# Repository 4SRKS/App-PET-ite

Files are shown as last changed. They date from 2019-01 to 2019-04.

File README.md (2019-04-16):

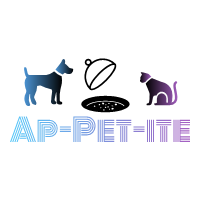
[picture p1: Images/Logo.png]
<br/>
## Social Media Profiles<br/>
[**Youtube**](https://www.youtube.com/channel/UCCG3uzNam2p5G15IFZl3F-A) 
[**Facebook**](https://www.facebook.com/Ap-PET-ite-2111281949162044/?view_public_for=2111281949162044)<br/>

## Project Overveiw<br/>
The basic layout of the project is given in the figure below<br/>
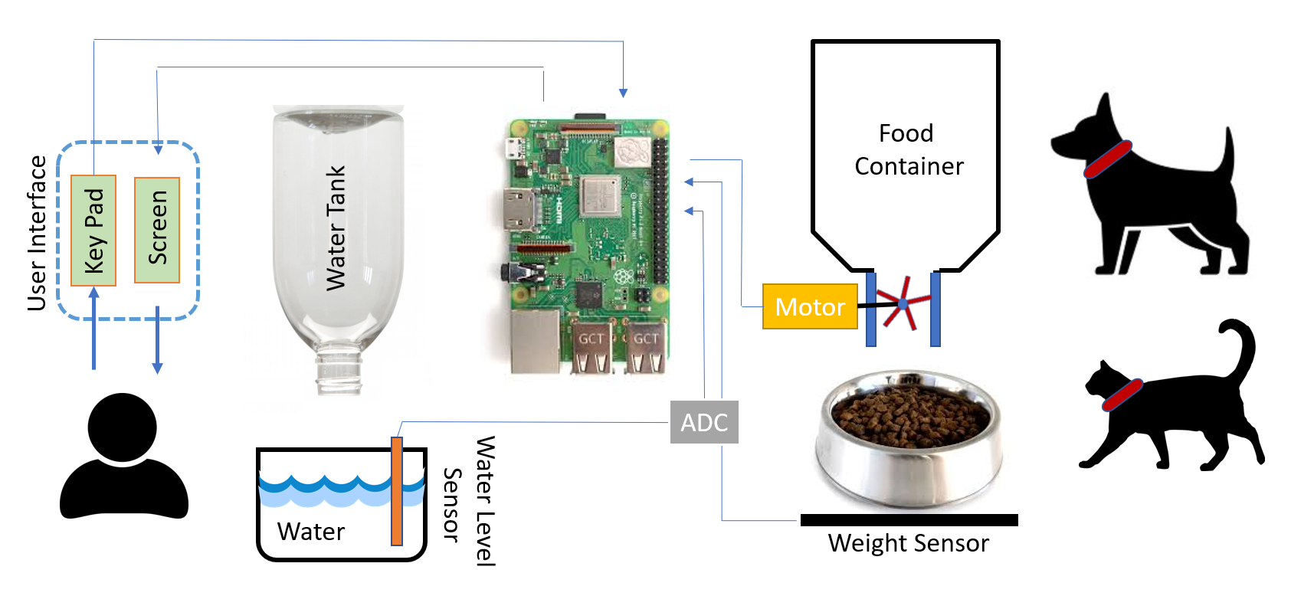
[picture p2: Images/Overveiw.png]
<br/>

## Project Description<br/>
The schematic above provides an overview of the project concept. The central component of the project design is a Raspberry Pi. The Pi is connected to peripheral devices that are used to control the food for a given Pet. The concept is not Pet specific and can be used to make an Automatic feeder for popular pets like cats or dogs and other smaller pets. The design includes two analog sensors to measure the weight and the water level. These sensors are connected to the Raspberry Pi through an ADC. SPI communication protocol is used to get analog values from the two sensors. A DC motor is controlled using a motor drive circuit. The user can interact with the Automatic Pet feeder through a user interface.<br/> 

## Component List<br/>
For this DIY project, we are using the Raspberry pi 3 Model B+ along with the following [Component List](https://github.com/RabiyaF/App-PET-ite/wiki/Component-List).<br/> <br/>
**Mechcanical Components List**<br/>
**1)** One DC Motor [6 Volts-150 RPM]<br/>
**2)** One Pet Food Bowl<br/> 
**3)** Wooden Planks<br/><br/>
**Electrical Components List** <br/>
**1)** One Analog water sensor<br/>
**2)** One Analog-to-digital Converter [MCP3008] <br/>
**3)** One 4x4 Matrix Keypad <br/>
**4)** One Analog Weight Sensor [HX711] with a maximum weight of 2 kgs <br/>
**5)** Five 1K Resistors <br/>
**6)** One TIP 122 or TIP 121 (NPN Transistor) <br/>
**7)** One LED <br/>
**8)** One Diode 1N4004 <br/>
**9)** Connector wires (F-F, M-F)<br/>
**10)** Two 20 Pin Female Connectors with a spacing of 0.1 in <br/>
**11)** One 8 pin Male connector with a spacing of 0.1 in <br/> 
**12)** One 4 pin Male connector with a spacing of 0.1 in <br/>
**13)** One 3 pin Male connector with a spacing of 0.1 in <br/>
**14)** One 16 pin IC holder with a spacing of 0.1 in between legs <br/>
After the Mechanical and Electrical Components have been procured, The following steps need to be followed to assemble App-PET-ite<br/>

# The Assembly 
## Mechanical Design Assembly <br/>
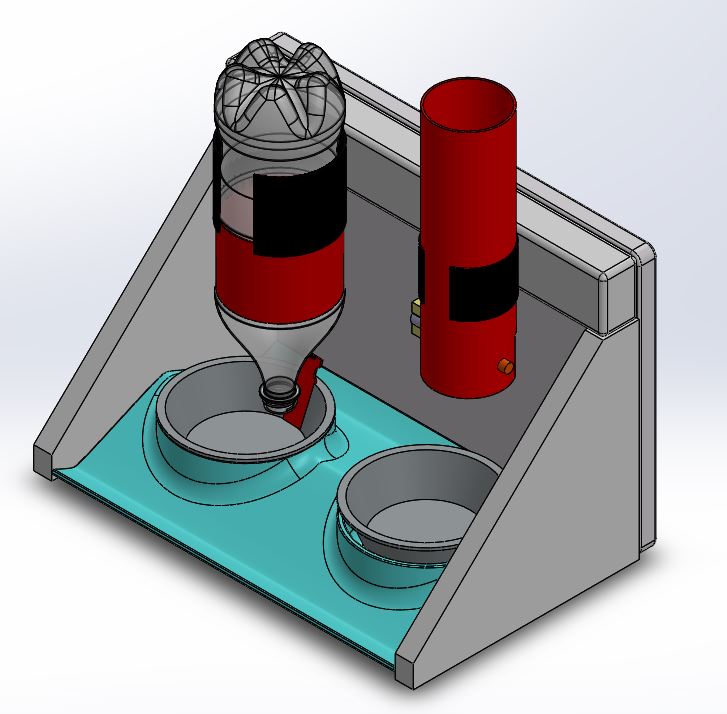
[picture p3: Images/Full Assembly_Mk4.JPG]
 <br/>
 <br/>
Shown above are a screenshot of the 3D CAD model and a photo of the final mechanical assembly.  The frame is made simply out of wood, and the clamps for the food and water tanks are made out of rigid PVC pipe with slots made in one side.  Everything else non-electrical is easily sourced in most supermarkets.  

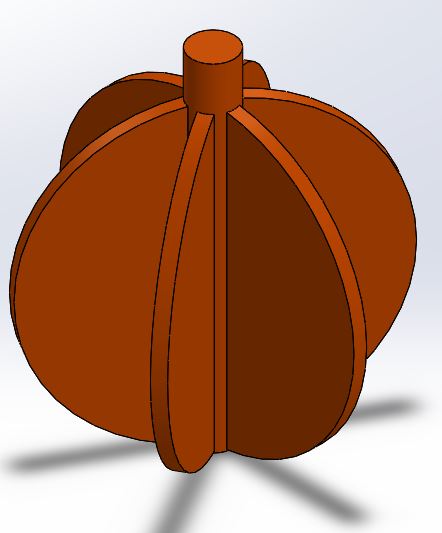
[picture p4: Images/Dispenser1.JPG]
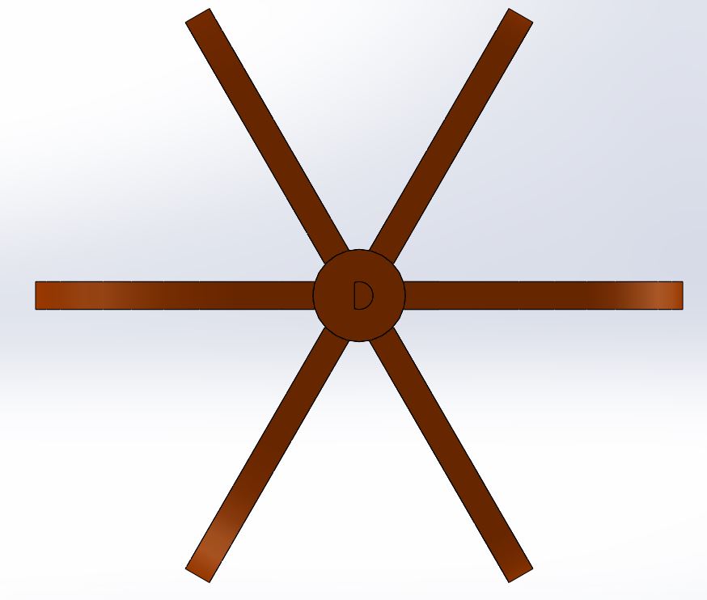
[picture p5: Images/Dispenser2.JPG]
 <br/>
The only other part requiring significant manufacturing is the dispenser mechanism, which was 3D printed.  Shown above are screenshots of this part.  For the .stl file of this component and the SolidWorks files of all the components shown in the full assembly, see the [SolidWorks/Mark 4](https://github.com/RabiyaF/App-PET-ite/tree/master/Solidworks/Mark%204) repository.  

For a full walkthrough of how we assembled the feeder, see the [Step-by-Step Assembly](https://github.com/RabiyaF/App-PET-ite/wiki/Step-by-Step-Mechanical-Assembly) page. <br/>

## Electrical Design Assembly <br/>
The first step of the electrical assembly is the PCB Fabrication.
### PCB Design <br/>
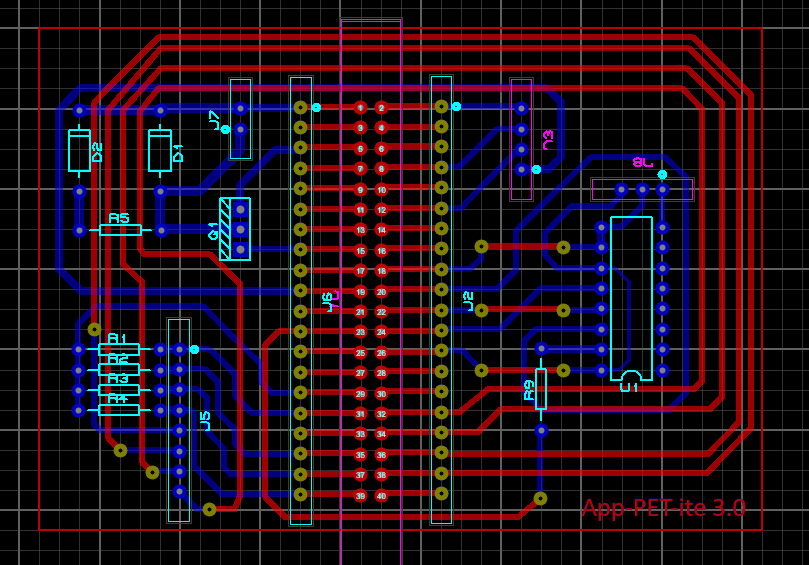
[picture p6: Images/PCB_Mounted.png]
<br/>
The figure above gives a preveiw of the PCB design. It is a double layered PCB Design. It includes the circuitry for Water Level Sensor, the ADC (MCP3008), the load cell (HX711), the key pad and the motordrive circuit. The PCB can be fabricated by printing the pdf files in the Double sided PCB folder and then using that layout to make a PCB step-by-step. A tutorial to make a PCB can be found at the following link. For a doubled layered PCB design the alignment of the two layers must be perfect. While aligning PCB use the text on the bottom as a guide to align the top and bottom halves. For a double sided PCB the process discribed in the tutorial must be repeated twice.<br/>
```
https://maker.pro/pcb/tutorial/how-to-make-a-printed-circuit-board-pcb
```
### Fabricated PCB<br/>
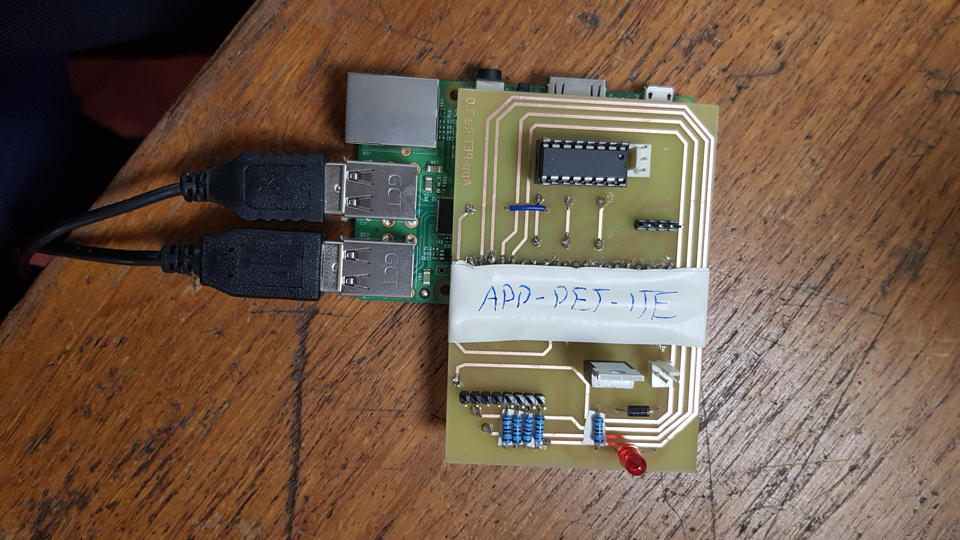
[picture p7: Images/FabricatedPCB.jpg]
<br/>

### Schematic<br/>
The figure below gives the schematic on which the PCB design is based.<br/>
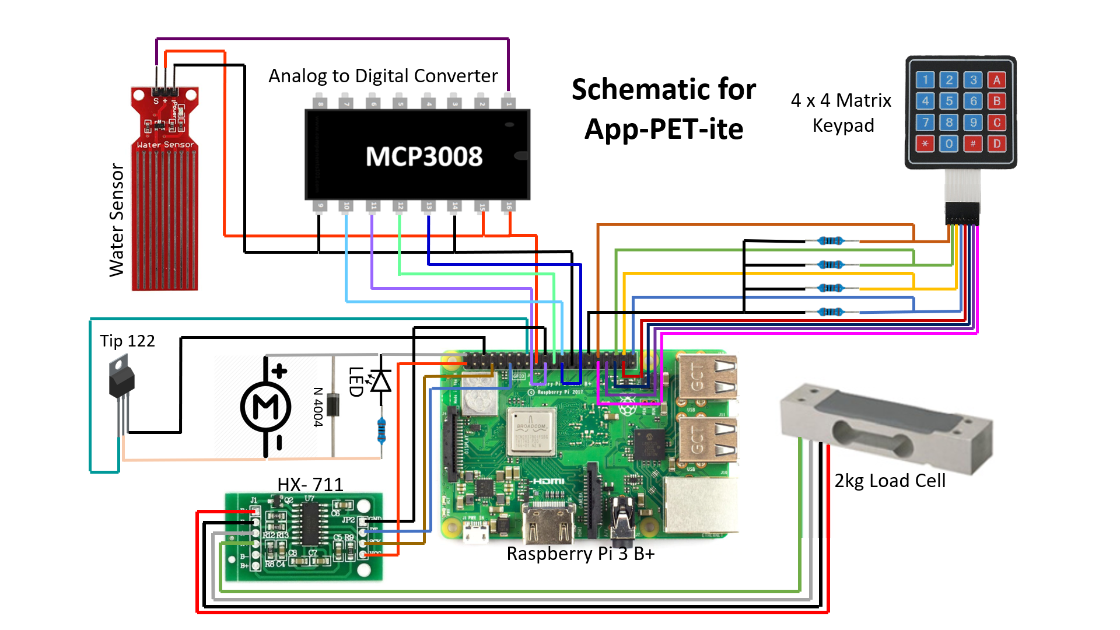
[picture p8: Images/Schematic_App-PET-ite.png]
<br/>

### Electrical Connections<br/>
A summary of the electrical connection is given below. <br/> 
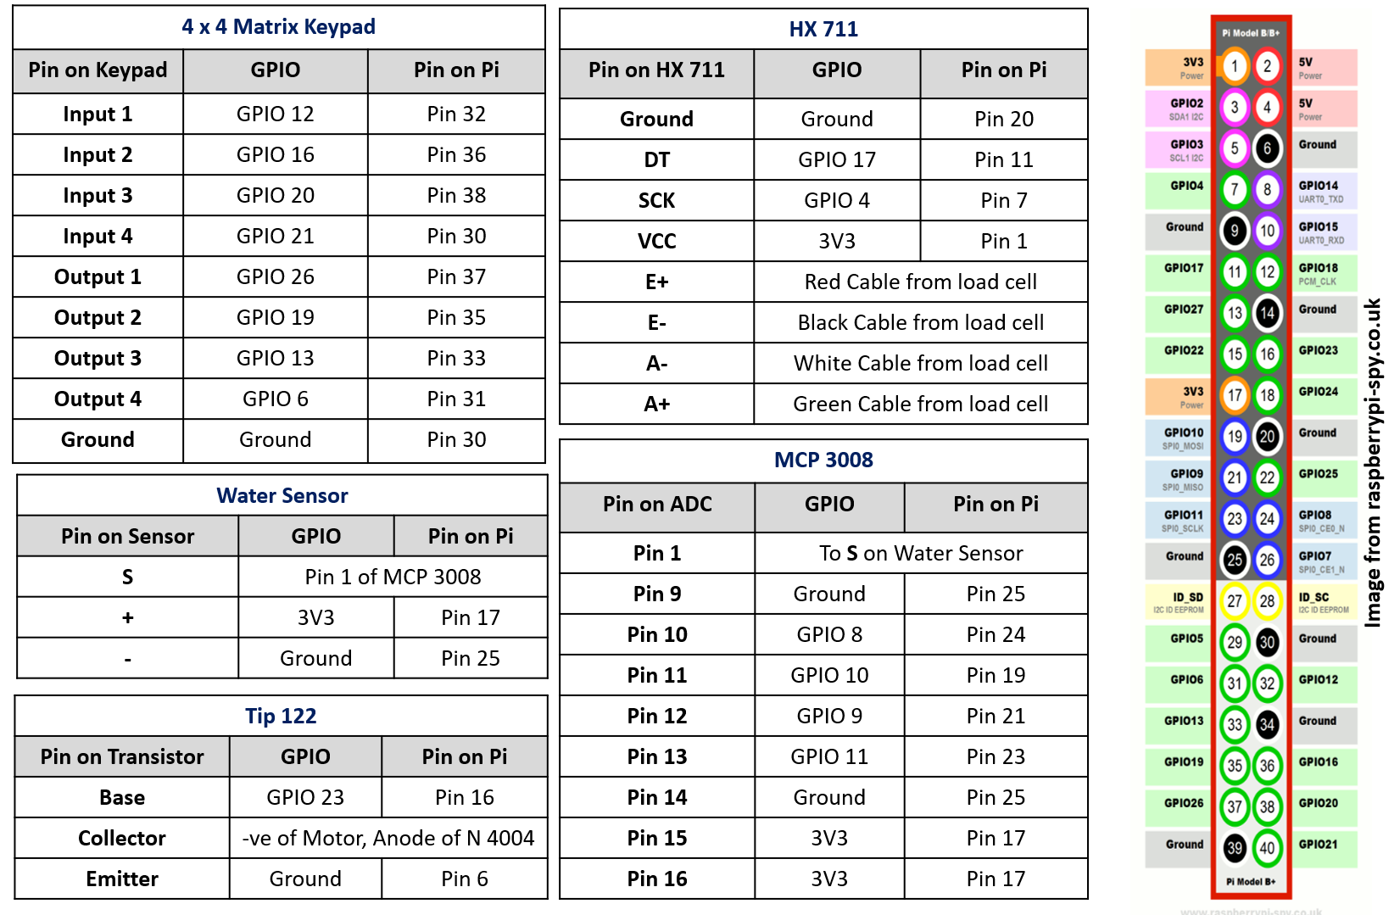
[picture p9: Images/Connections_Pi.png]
<br/>

## Ensuring Safety of Pet<br/>
Because of the nature of the project, It is recommneded to use the PCB layouts rather than using the schematic to build the circuit on a breadboard. All the wires must be taped down and all the electrical components should be out of the reach of the Pet. 

## Flowchart<br/>
The Flow chart below gives the overveiw of the code. First, the user initializes App-PET-ite with inputs for weight and time between two subsequent feeding times. The food is then dispensed based on user input. Then two threads run simulataneously. One counts down to the next time food is to be dispensed. The other thread periodically measures the Water level.  
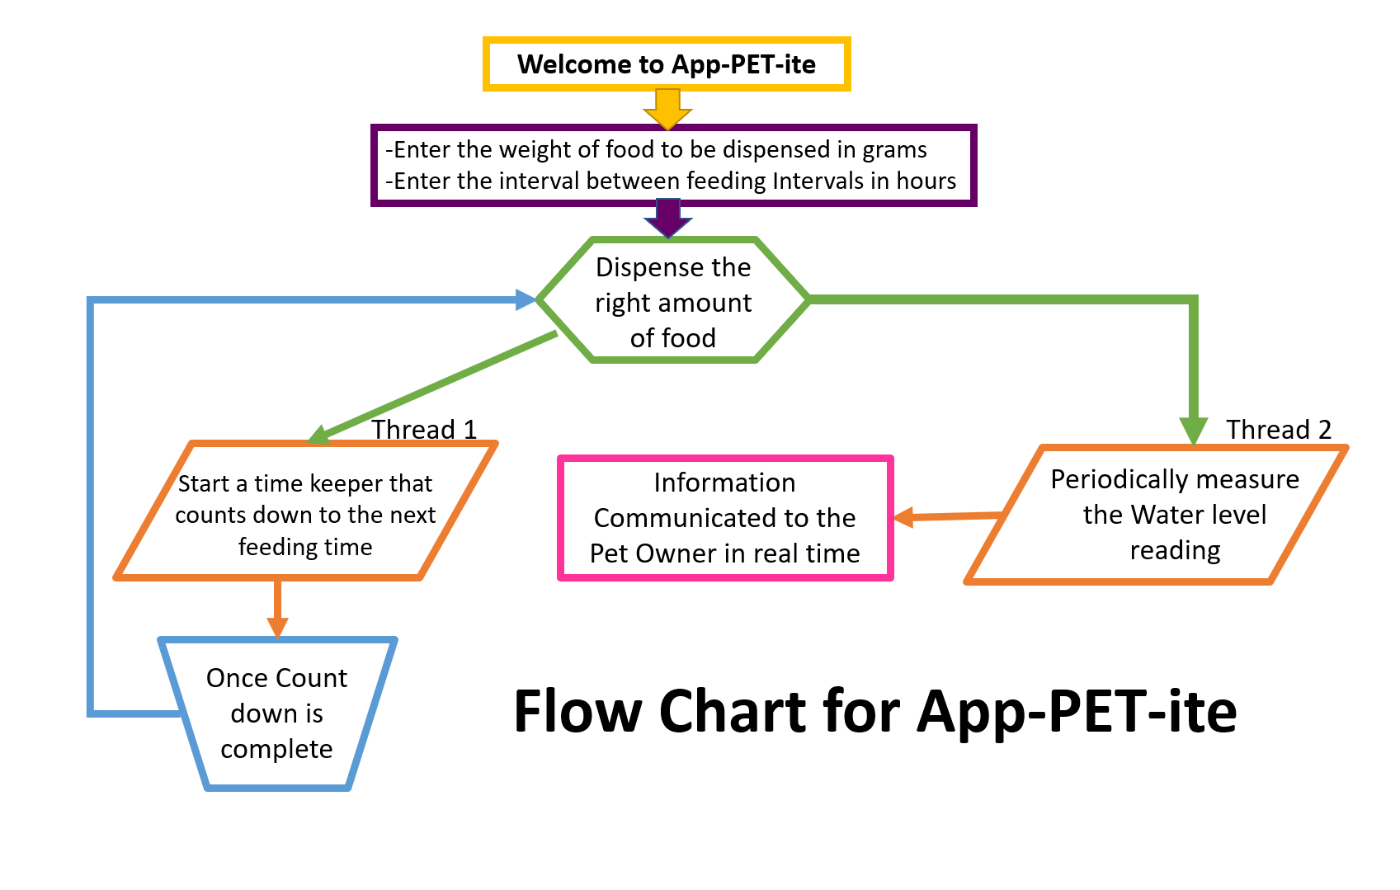
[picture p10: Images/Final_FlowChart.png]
<br/>

## Install the following packages using sudo apt-get <package name>
```
git 2.21.0
cmake-3.14.2.tar.gz
Qt 4.8.7
```
## To Run
```
git clone https://github.com/RabiyaF/App-PET-ite
cd Final_codes/build
cmake ..
make
./mypjex
```

## User Interface
The user interface is given below. First, the user is promted to enter the weight of food to be dispensed in hours. Then the user is promted to enter the time between subsequent feedings. Then the user is asked verify the data entry. Once the data is entered, the correct amount of food will be dispensed after the specified time intervals for the Pet to enjoy and no further input is needed from the Pet owner after that. <br/>  
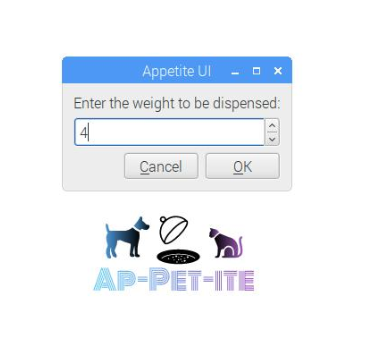
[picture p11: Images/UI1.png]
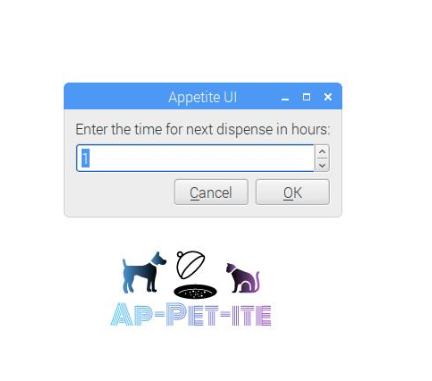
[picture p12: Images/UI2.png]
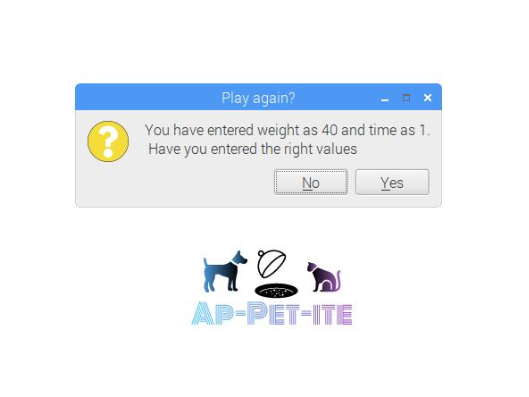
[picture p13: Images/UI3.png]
    <br/>  

## Reporting a Bug
Use this link-[App-PET-ite Bug](https://github.com/RabiyaF/App-PET-ite/issues) to contact the team members to fix issues with software. <br/>

## License
GNU General Public License V3<br/>
GNU LESSER GENERAL PUBLIC LICENSE V3<br/>

## Team Members

* **Raghul** <br/> 
*Initial Concept Contribution* -App-PET-ite logo <br/>
2.Load cell setup and configuration<br/>
3.UI interface, repository maintenance.<br/>
4.Integration testing, Unit testing<br/>
* **Stuart Shilliday** <br/>
*Initial Concept Contribution* - Concept pitch presentation <br/>
*Mechanical Contribution* - Design, manufacture, iteration and assembly.  Step-by-Step Mechanical Assembly Wiki <br/>
*Social Media Contribution* - YouTube and Facebook pages; photography, videography, video editing and uploading <br/>
* **Rabiya Farooq**<br/> 
*Initial Concept Contribution* - Slides for pitch presentation <br/>
*Programming Contribution-* The ADC (MCP3008) for water level sensing, 4x4 Matrix Keypad, Motordrive control and threads for Water level sensor and timer <br/>
*Electronic Contribution-* Double layered PCB design on Proteus Design Suite Professional v8.7, Soldering, testing and debugging of PCB Hardware <br/>

## Survey
PLease participate in this survey to give insight and feedback on Ap-PET-ite for future releases.<br/>
[Ap-PET-ite Survey](https://docs.google.com/forms/d/e/1FAIpQLSdCzQ5AlhaeOhvKFN2g8C_C-drHnjaCQEvHc7EBsoWmiBpvOg/viewform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)

## Release Strategy
**Ap-PET-ite v1.0**
* Dispenses food of given mass at given intervals, and maintains water level, with inputs given from a UI. <br/>
Release date - 15th April 2019 <br/>

**Ap-PET-ite v2.0** 
* Depending on Survey results and general feedback, Version 2 will have following aditional funtionalities  <br/>
**1)** RFID Sensor (MFRC 522) for Pet identification and differentiation to allow feeding to be customized for each pet in a multipet household  <br/>and/or  <br/>
**2)** LCD Screen (ST 7735 128x160 pixel 1.8 inch Display) for the user to input and update the setting directly on to the Ap-PET-ite hardware <br/>

**Ap-PET-ite v3.0**
* The last version will enable an exclusive Mobile App and an ASIC chip and will be marketed for a commercial release.

## Acknowledgements
The follwing libraries were used to build the code
```
https://github.com/berndporr/gpio-sysfs
https://github.com/halherta/RaspberryPi-mcp3008Spi
https://github.com/dangrie158/opencushion
https://git.drogon.net/?p=wiringPi;a=summary
```

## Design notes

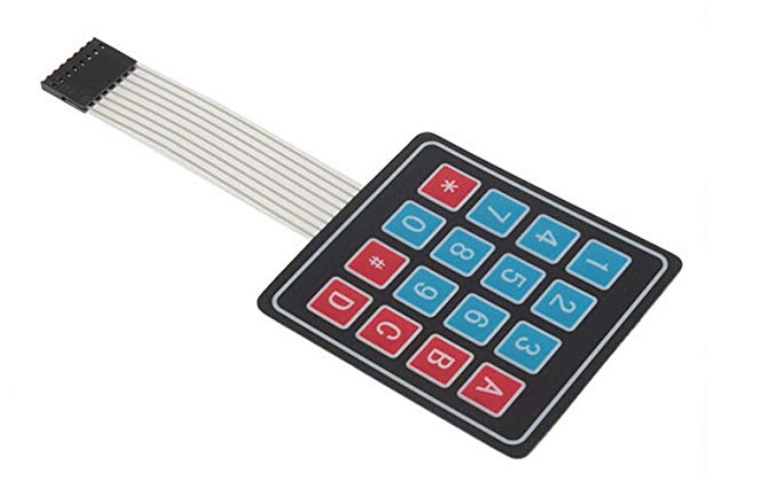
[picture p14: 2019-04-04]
Images/MatrixKeyPad.png

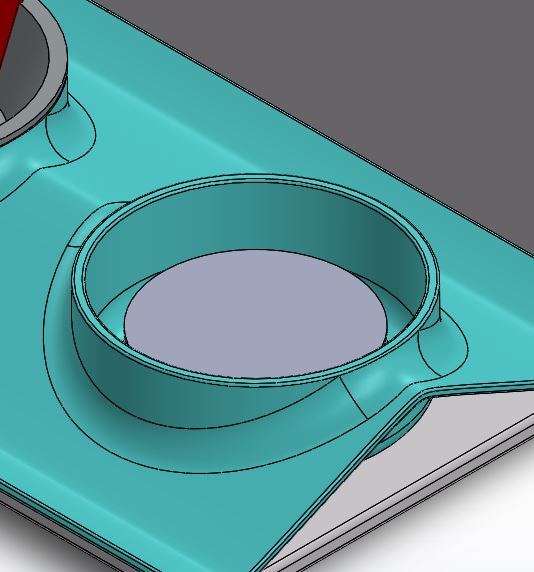
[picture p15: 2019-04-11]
Images/Load_Cell.JPG

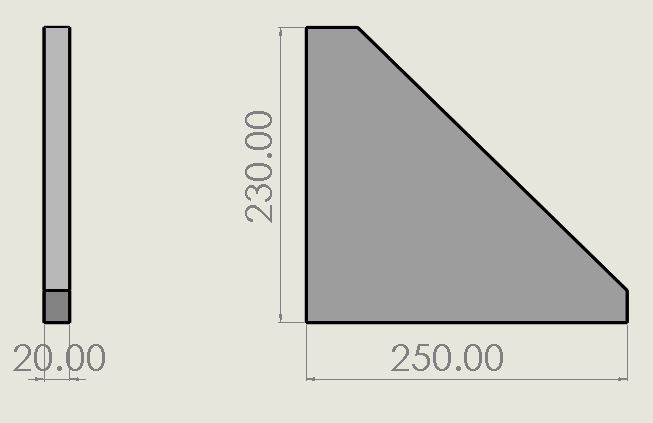
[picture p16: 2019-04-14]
Images/Side_Board_Dimensions.JPG

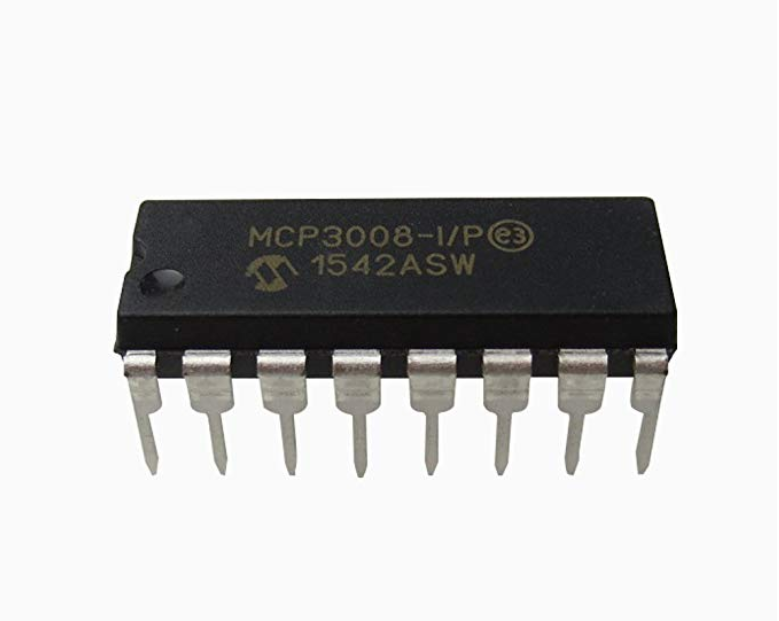
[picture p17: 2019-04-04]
Images/MCP3008.png

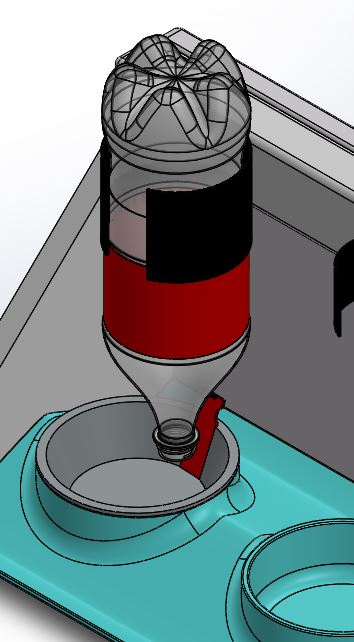
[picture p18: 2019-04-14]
Images/Water_Dispenser_System_Mk4.JPG

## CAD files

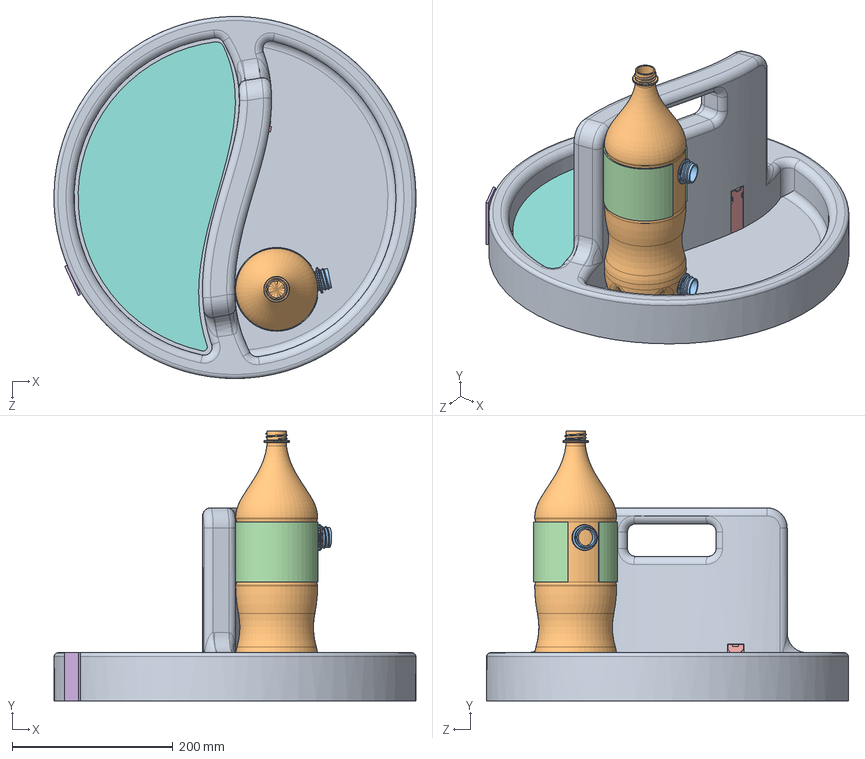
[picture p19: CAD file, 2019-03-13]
Solidworks/Full_Assembly.SLDASM
449.9 x 335.5 x 450.0 mm
Feeding_Bowl_Mk1
2l_cola_bottle
Cola_Cap x 2
Bottle_Holder
Water Sensor
RFID_Sensor
Load_Cell
Food_Plate

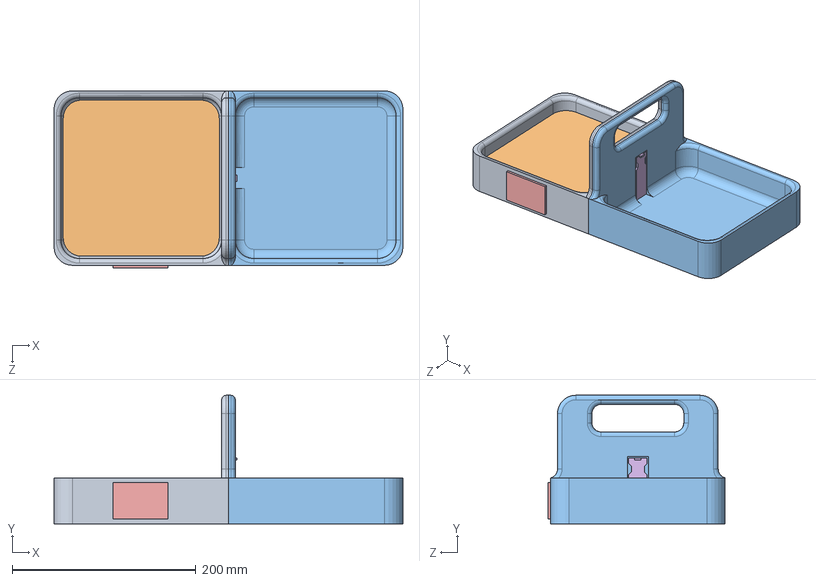
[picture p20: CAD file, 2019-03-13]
Solidworks/Full_Assembly_Mk2.SLDASM
380.0 x 140.0 x 193.0 mm
Food_Bowl
Food_Plate_Mk2
Water_Bowl
Load_Cell
RFID_Sensor
Water Sensor

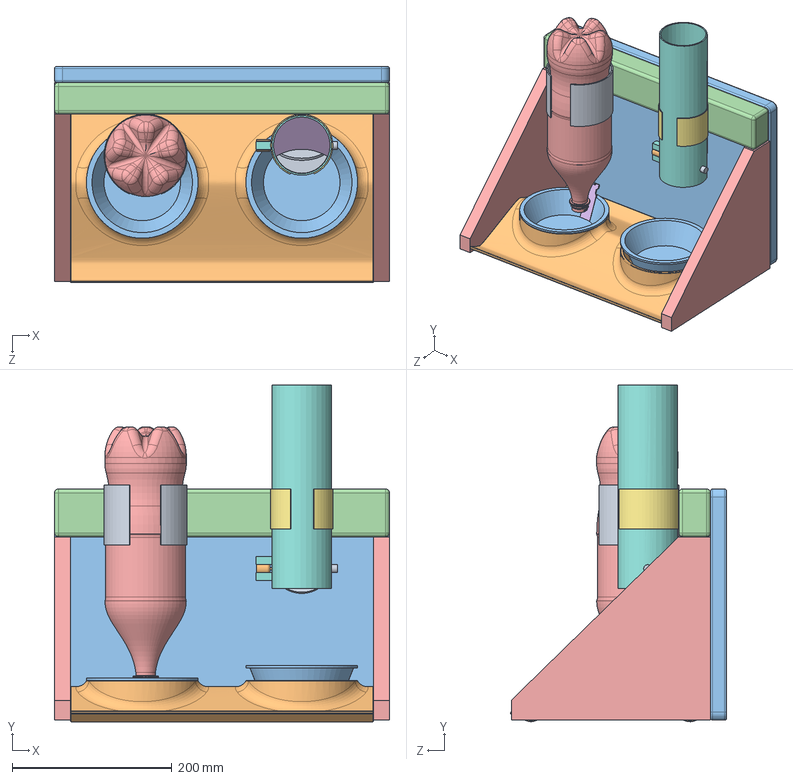
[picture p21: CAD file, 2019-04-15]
Solidworks/Mark 4/Full Assembly Mk4.SLDASM
420.0 x 422.0 x 271.1 mm
Bottle_Holder
Bowl Bottom
Bowl x 2
Load_Cell
2l_cola_bottle
Water Sensor
Can Holder
Pringles Can
Food_Dispenser
Motor
Back Plate
Top Frame
Side x 2
Funnel

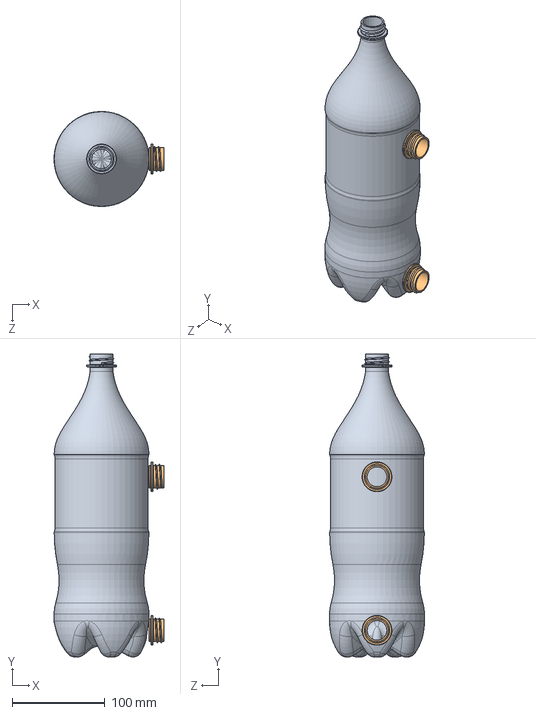
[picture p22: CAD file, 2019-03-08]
Solidworks/Water_Tank.SLDASM
118.5 x 326.5 x 102.4 mm
2l_cola_bottle
Cola_Cap x 2

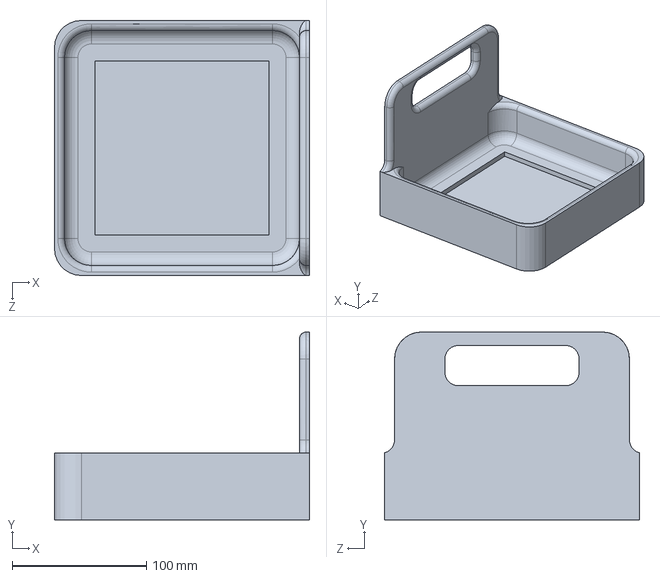
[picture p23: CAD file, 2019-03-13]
Solidworks/Food_Bowl.SLDPRT
190.0 x 140.0 x 190.0 mm

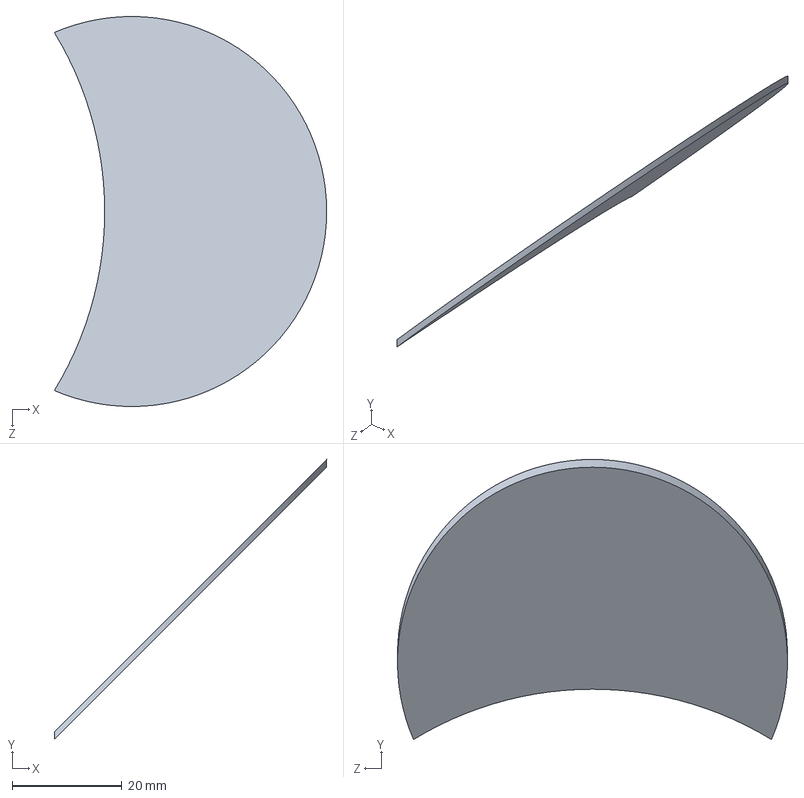
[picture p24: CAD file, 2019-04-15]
Solidworks/Mark 4/Funnel.SLDPRT
49.6 x 51.0 x 71.0 mm

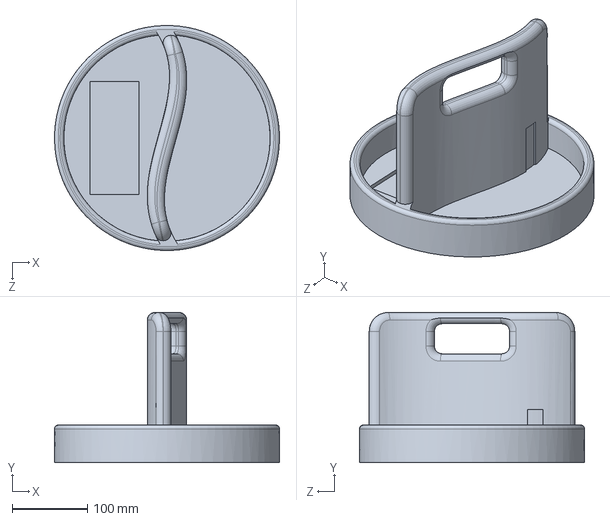
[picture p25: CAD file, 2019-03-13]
Solidworks/Feeding_Bowl_Mk2.SLDPRT
300.0 x 200.0 x 300.0 mm

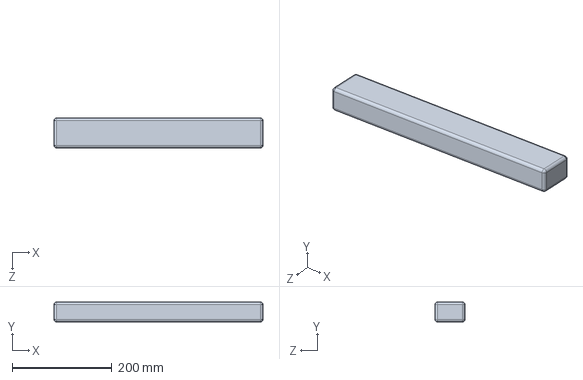
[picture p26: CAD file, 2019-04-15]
Solidworks/Mark 4/Top Frame.SLDPRT
420.0 x 40.0 x 60.0 mm

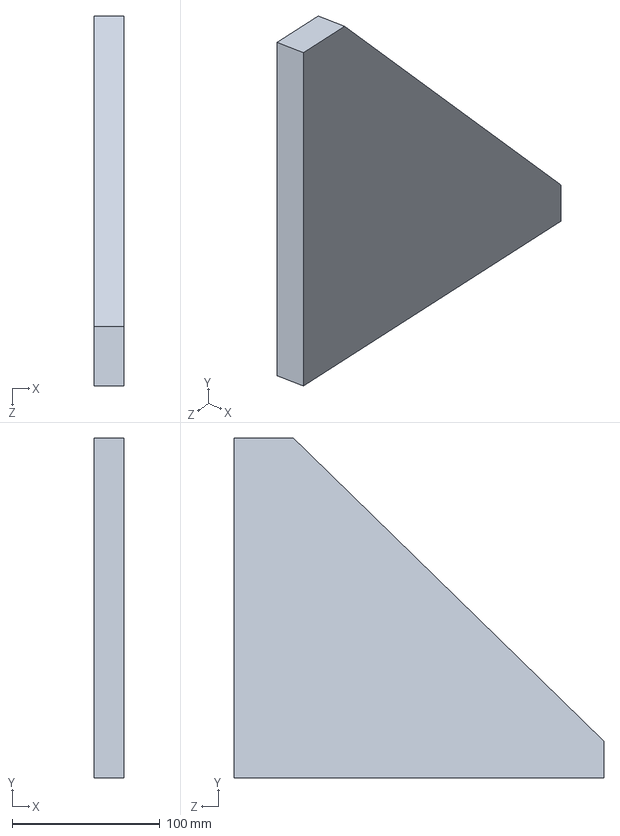
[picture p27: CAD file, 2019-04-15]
Solidworks/Mark 4/Side.SLDPRT
20.0 x 230.0 x 250.0 mm

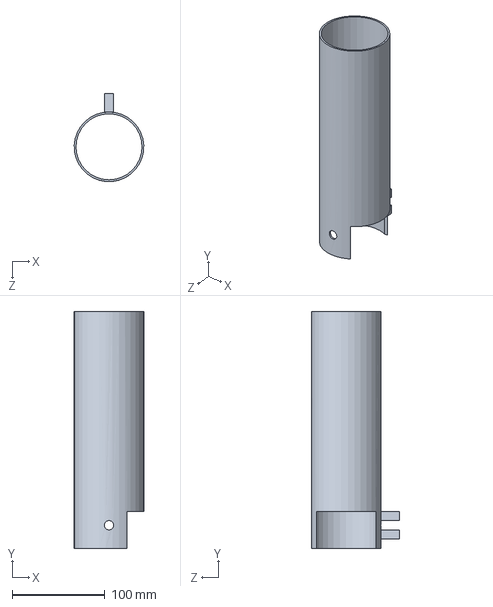
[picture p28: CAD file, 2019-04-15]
Solidworks/Mark 4/Pringles Can.SLDPRT
74.9 x 255.0 x 95.0 mm

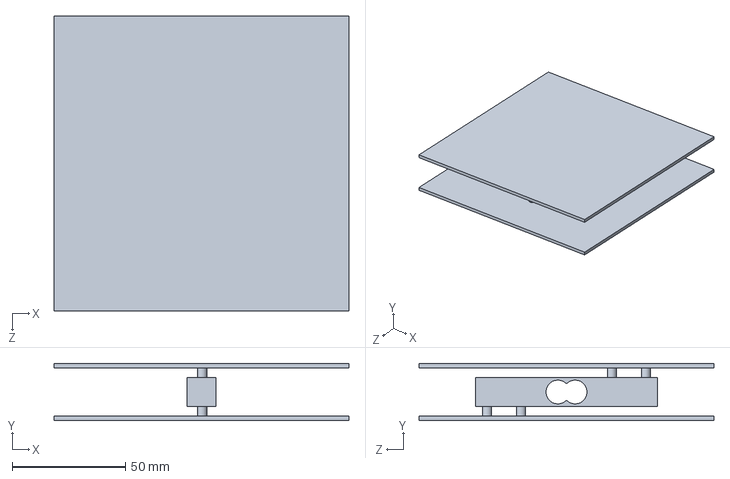
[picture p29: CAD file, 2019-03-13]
Solidworks/Load_Cell.SLDPRT
130.0 x 25.3 x 130.0 mm

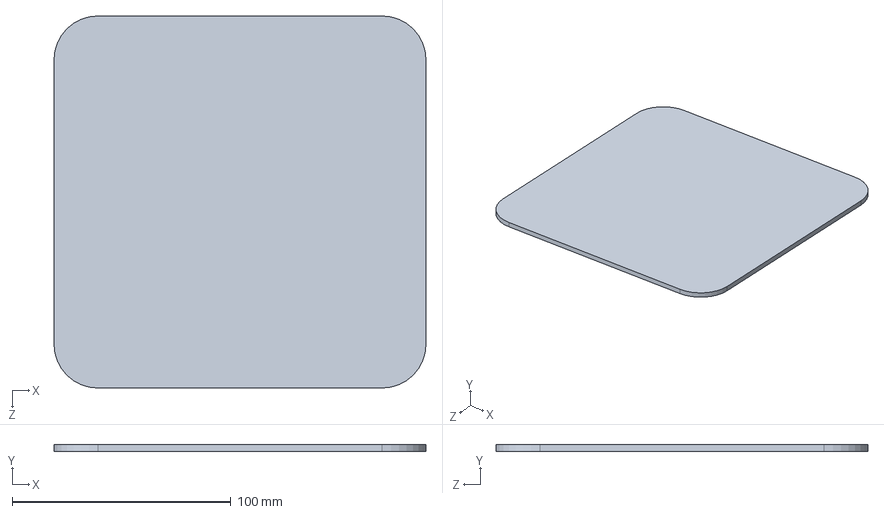
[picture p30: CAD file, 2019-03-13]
Solidworks/Food_Plate_Mk2.SLDPRT
170.0 x 3.00 x 170.0 mm

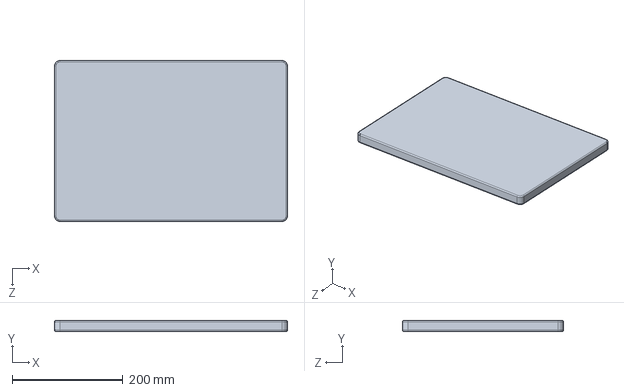
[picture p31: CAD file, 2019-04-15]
Solidworks/Mark 4/Back Plate.SLDPRT
420.0 x 20.0 x 290.0 mm

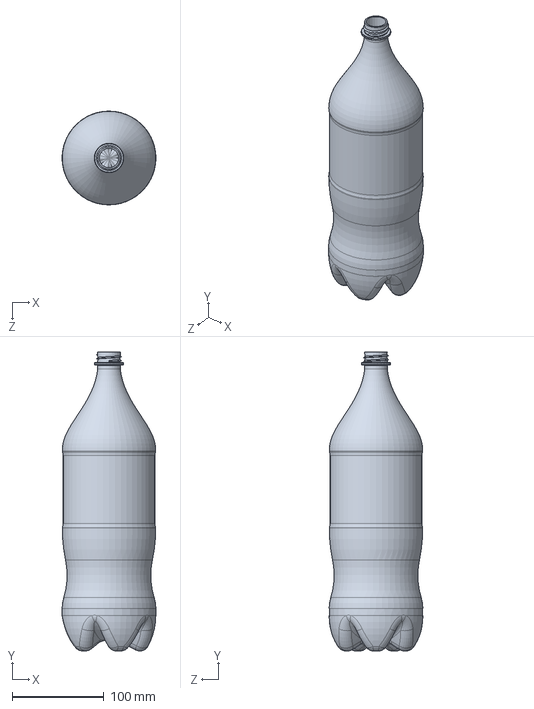
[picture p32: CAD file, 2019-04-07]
Solidworks/Mark 4/2l_cola_bottle.SLDPRT
102.4 x 326.5 x 102.4 mm

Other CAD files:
Solidworks/Water_Bowl.SLDPRT
Solidworks/Feeding_Bowl_Mk1.SLDPRT
Solidworks/Mark 4/Load_Cell.SLDPRT
Solidworks/Mark 4/Food_Dispenser.SLDPRT
Solidworks/2l_cola_bottle.SLDPRT
Solidworks/Bottle_Holder.SLDPRT
Solidworks/Cola_Cap.SLDPRT
Solidworks/Feeding_Bowl_Mk1.STL
Solidworks/Food_Bowl.STL
Solidworks/Food_Plate.SLDPRT
Solidworks/Food_Plate_Mk2.STL
Solidworks/Mark 3/Back Plate.SLDPRT
Solidworks/Mark 3/Full Assembly Mk3.SLDASM
Solidworks/Mark 3/Pringles Can.SLDPRT
Solidworks/Mark 3/Top Frame.SLDPRT
Solidworks/Mark 4/Base.SLDPRT
Solidworks/Mark 4/Bottle_Holder.SLDPRT
Solidworks/Mark 4/Bowl Bottom.SLDPRT
Solidworks/Mark 4/Bowl.SLDPRT
Solidworks/Mark 4/Can Holder.SLDPRT
Solidworks/Mark 4/Food_Dispenser.STL
Solidworks/Mark 4/Motor.SLDPRT
Solidworks/Mark 4/RFID_Sensor.SLDPRT
Solidworks/Mark 4/Water Sensor.SLDPRT
Solidworks/Motor.SLDPRT
Solidworks/Water_Bowl.STL

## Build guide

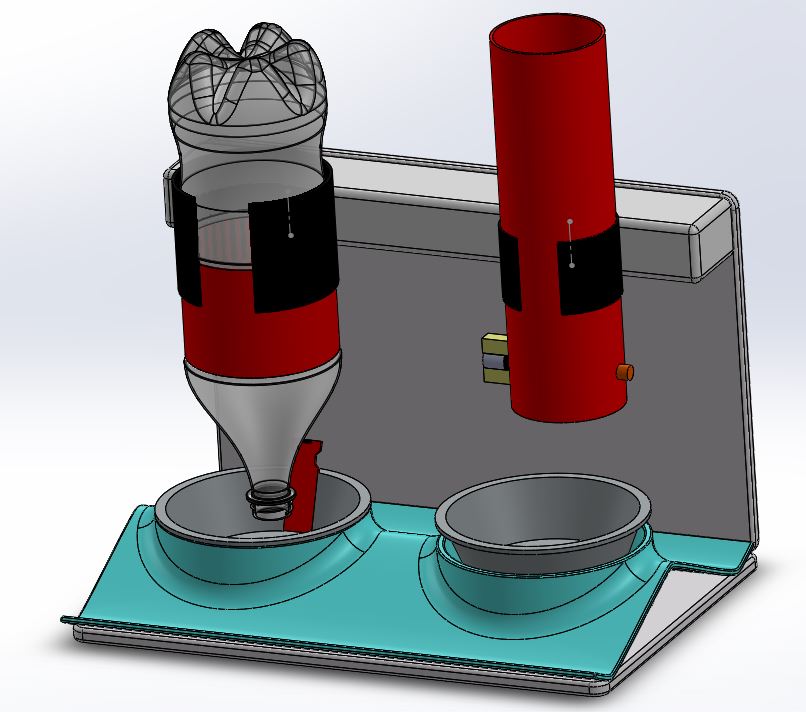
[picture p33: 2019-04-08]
Images/Full Assembly.JPG

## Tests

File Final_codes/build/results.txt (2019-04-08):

Scanning dependencies of target mypjex
[ 50%] Building CXX object CMakeFiles/mypjex.dir/thread.cpp.o
[100%] Linking CXX executable mypjex
[100%] Built target mypjex

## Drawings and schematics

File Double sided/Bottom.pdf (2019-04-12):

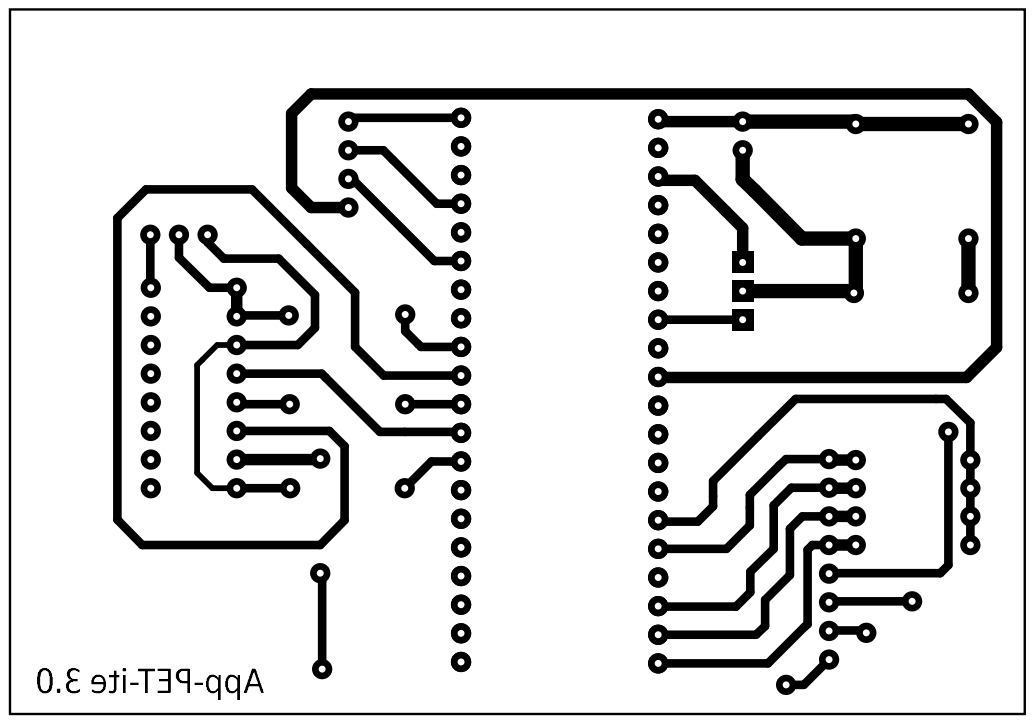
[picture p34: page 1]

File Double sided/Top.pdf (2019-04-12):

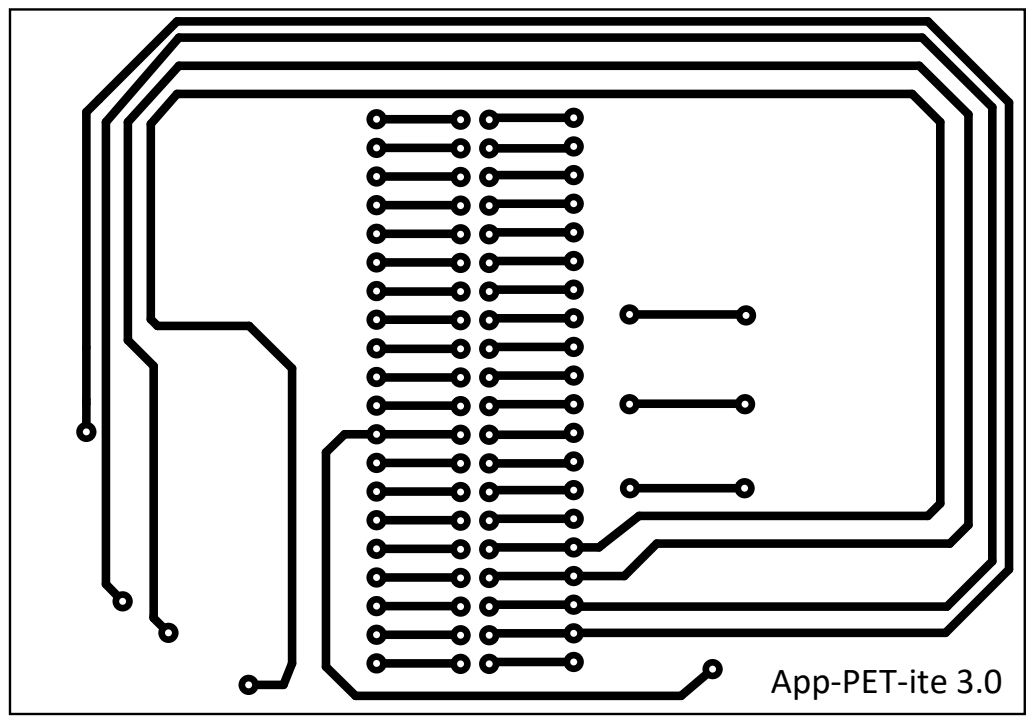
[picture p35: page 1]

App-PET-ite 3.0

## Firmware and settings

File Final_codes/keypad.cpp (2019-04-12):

/********************
* The header files
*********************/
#include <stdint.h>
#include <unistd.h>
#include <stdio.h>
#include <stdlib.h>
#include <fcntl.h>
#include <sys/ioctl.h>
#include <linux/types.h>
#include <linux/spi/spidev.h>
#include <iostream>
using namespace std;

/*************************************************************************************************************************************
* Using the following libraries from https://github.com/berndporr/gpio-sysfs to set the GPIOs as Inputs and Outputs for the Keypad
**************************************************************************************************************************************/
#include "gpio-sysfs.h"
#include "gpio-sysfs.cpp"

/**************************************************************************************************************************************************************
* Keypad function declaration that initializes the Inputs and Outputs and then waits for a key to be pressed and then returns the value of the key pressed 
***************************************************************************************************************************************************************/
int keypad(unsigned int in1, unsigned int in2, unsigned int in3, unsigned int in4, unsigned int out1, unsigned int out2, unsigned int out3, unsigned int out4){
/************************************      
* Declaring the output GPIOs
*************************************/
unsigned int drdy5_GPIO = out1;
unsigned int drdy6_GPIO = out2;
unsigned int drdy7_GPIO = out3;
unsigned int drdy8_GPIO = out4;

/************************************
* Declaring the input GPIOs
*************************************/
unsigned int drdy1_GPIO = in4;
unsigned int drdy2_GPIO = in3;
unsigned int drdy3_GPIO = in2;
unsigned int drdy4_GPIO = in1;

/*************************************************************************
* Gpio-sysfs uses pointers to store the value of the Inputs
* So declaring the pointer where the keypad input values will be stored
**************************************************************************/
unsigned int *sysfs_fd1;
unsigned int *sysfs_fd2;
unsigned int *sysfs_fd3;
unsigned int *sysfs_fd4;

/****************************************************************
* Varibles to associate the addresses to the sysfs variables
*****************************************************************/
unsigned int value1;
unsigned int value2;
unsigned int value3;
unsigned int value4;

/***********************************************************************************************
* Allocating addresses of variables to the pointers. This is done to avoid segmentation fault
************************************************************************************************/
sysfs_fd1=&value1;
sysfs_fd2=&value2;
sysfs_fd3=&value3;
sysfs_fd4=&value4;
        
/**************************************
* Exporting the GPIOs
***************************************/
gpio_export(drdy5_GPIO);
gpio_export(drdy6_GPIO);
gpio_export(drdy7_GPIO);
gpio_export(drdy8_GPIO);

/**************************************
* Setting the GPIOs as Output
***************************************/
gpio_set_dir(drdy5_GPIO,1);
gpio_set_dir(drdy6_GPIO,1);
gpio_set_dir(drdy7_GPIO,1);
gpio_set_dir(drdy8_GPIO,1);

/**************************************
* Initializing the Output values as 0
***************************************/
gpio_set_value(drdy5_GPIO,0);               
gpio_set_value(drdy6_GPIO,0);               
gpio_set_value(drdy7_GPIO,0);
gpio_set_value(drdy8_GPIO,0);                
                
/**************************************
* Exporting the GPIOs
***************************************/
gpio_export(drdy1_GPIO);
gpio_export(drdy2_GPIO);                
gpio_export(drdy3_GPIO);                
gpio_export(drdy4_GPIO);                

/**************************************
* Setting GPIOs as input
***************************************/          
gpio_set_dir(drdy1_GPIO,0);
gpio_set_dir(drdy2_GPIO,0);
gpio_set_dir(drdy3_GPIO,0);
gpio_set_dir(drdy4_GPIO,0);

/**************************************               
* Declaring Array of Keppad Buttons
***************************************/
char keys[4][4]={{'1','2','3','A'},
                 {'4','5','6','B'},
                 {'7','8','9','C'},
                 {'*','0','#','D'}};
int keys_ret[4][4]={{1,2,3,12},
                    {4,5,6,13},
                    {7,8,9,14},
                    {10,0,11,15}};
int myval=0;
int val;
unsigned int outputs[4]={drdy5_GPIO,drdy6_GPIO,drdy7_GPIO,drdy8_GPIO};
unsigned int inputs[4]={drdy4_GPIO,drdy3_GPIO,drdy2_GPIO,drdy1_GPIO};
unsigned int *sys[4]={sysfs_fd4,sysfs_fd3,sysfs_fd2,sysfs_fd1};
int p=1;
        
/******************************************************************************************************************
* Defining the nested for loop that sequentially changes the value of the four outputs to Logic 1
* Once the output value is set to 1, the input values are checked one by one
* The input should be Logic 0 (because of the Pull down resistors) when no key is pressed
* The input turns to logic 1 when a key is pressed
* Depending on which output was 1 when a certain input became 1, the key which was pressed can be identified
* Once the key identified the return value is updated
* The loop breaks afte the first key is pressed.
* This function allows only one key pressed to be recognized.
* To get continous input from the Keypad, this fuction must be called continously
*******************************************************************************************************************/
while(p)
      {
      for (int t=0; t<=3; t++)
        {
        gpio_set_value(outputs[t],1);
        for (int k=0; k<=3; k++)
                {
                val=gpio_get_value(inputs[k],sys[k]);
                if(*sys[k]==1)
                        {
                        myval=keys_ret[k][t];
                        //cout<<keys[k][t]<<endl;
                        usleep(500000); //The delay is added to avoid multiple positive results when pressing the key once
                        p=0;
                        }
                 }
         gpio_set_value(outputs[t],0);
         }
      }
return myval;
}
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

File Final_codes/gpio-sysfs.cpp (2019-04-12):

/*************************************************************************************************************************
* The following library for setting GPIOs as inputs and outputs can be found at https://github.com/berndporr/gpio-sysfs 
**************************************************************************************************************************/

/* Copyright (c) 2011, RidgeRun
 * Copyright (c) 2014, Bernd Porr
 * All rights reserved.
 * 
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
 * THIS SOFTWARE IS PROVIDED BY RIDGERUN ''AS IS'' AND ANY
 * EXPRESS OR IMPLIED WARRANTIES, INCLUDING, BUT NOT LIMITED TO, THE IMPLIED
 * WARRANTIES OF MERCHANTABILITY AND FITNESS FOR A PARTICULAR PURPOSE ARE
 * DISCLAIMED. IN NO EVENT SHALL RIDGERUN BE LIABLE FOR ANY
 * DIRECT, INDIRECT, INCIDENTAL, SPECIAL, EXEMPLARY, OR CONSEQUENTIAL DAMAGES
 * (INCLUDING, BUT NOT LIMITED TO, PROCUREMENT OF SUBSTITUTE GOODS OR SERVICES;
 * LOSS OF USE, DATA, OR PROFITS; OR BUSINESS INTERRUPTION) HOWEVER CAUSED AND
 * ON ANY THEORY OF LIABILITY, WHETHER IN CONTRACT, STRICT LIABILITY, OR TORT
 * (INCLUDING NEGLIGENCE OR OTHERWISE) ARISING IN ANY WAY OUT OF THE USE OF THIS
 * SOFTWARE, EVEN IF ADVISED OF THE POSSIBILITY OF SUCH DAMAGE.
 */

#include <stdio.h>
#include <stdlib.h>
#include <string.h>
#include <errno.h>
#include <unistd.h>
#include <fcntl.h>
#include <poll.h>

#include "gpio-sysfs.h"

/****************************************************************
 * Constants
 ****************************************************************/
 
#define SYSFS_GPIO_DIR "/sys/class/gpio"

/****************************************************************
 * gpio_export
 ****************************************************************/
int gpio_export(unsigned int gpio)
{
  int fd, len;
  char buf[MAX_BUF];
 
  fd = open(SYSFS_GPIO_DIR "/export", O_WRONLY);
  if (fd < 0) {
    perror("gpio/export");
    return fd;
  }
 
  len = snprintf(buf, sizeof(buf), "%d", gpio);
  write(fd, buf, len);
  close(fd);
 
  return 0;
}

/****************************************************************
 * gpio_unexport
 ****************************************************************/
int gpio_unexport(unsigned int gpio)
{
  int fd, len;
  char buf[MAX_BUF];
 
  fd = open(SYSFS_GPIO_DIR "/unexport", O_WRONLY);
  if (fd < 0) {
    perror("gpio/export");
    return fd;
  }
 
  len = snprintf(buf, sizeof(buf), "%d", gpio);
  write(fd, buf, len);
  close(fd);
  return 0;
}

/****************************************************************
 * gpio_set_dir
 ****************************************************************/
int gpio_set_dir(unsigned int gpio, unsigned int out_flag)
{
  int fd;
  char buf[MAX_BUF];
 
  snprintf(buf, sizeof(buf), SYSFS_GPIO_DIR  "/gpio%d/direction", gpio);
 
  fd = open(buf, O_WRONLY);
  if (fd < 0) {
    perror("gpio/direction");
    return fd;
  }
 
  if (out_flag)
    write(fd, "out", 4);
  else
    write(fd, "in", 3);
 
  close(fd);
  return 0;
}

/****************************************************************
 * gpio_set_value
 ****************************************************************/
int gpio_set_value(unsigned int gpio, unsigned int value)
{
  int fd;
  char buf[MAX_BUF];
 
  snprintf(buf, sizeof(buf), SYSFS_GPIO_DIR "/gpio%d/value", gpio);
 
  fd = open(buf, O_WRONLY);
  if (fd < 0) {
    perror("gpio/set-value");
    return fd;
  }
 
  if (value)
    write(fd, "1", 2);
  else
    write(fd, "0", 2);
 
  close(fd);
  return 0;
}

/****************************************************************
 * gpio_get_value
 ****************************************************************/
int gpio_get_value(unsigned int gpio, unsigned int *value)
{
  int fd;
  char buf[MAX_BUF];
  char ch;

  snprintf(buf, sizeof(buf), SYSFS_GPIO_DIR "/gpio%d/value", gpio);
 
  fd = open(buf, O_RDONLY);
  if (fd < 0) {
    perror("gpio/get-value");
    return fd;
  }
 
  read(fd, &ch, 1);

  if (ch != '0') {
    *value = 1;
  } else {
    *value = 0;
  }
 
  close(fd);
  return 0;
}


/****************************************************************
 * gpio_set_edge
 ****************************************************************/

int gpio_set_edge(unsigned int gpio, const char *edge)
{
  int fd;
  char buf[MAX_BUF];

  snprintf(buf, sizeof(buf), SYSFS_GPIO_DIR "/gpio%d/edge", gpio);
 
  fd = open(buf, O_WRONLY);
  if (fd < 0) {
    perror("gpio/set-edge");
    return fd;
  }
 
  write(fd, edge, strlen(edge) + 1); 
  close(fd);
  return 0;
}

/****************************************************************
 * gpio_fd_open
 ****************************************************************/

int gpio_fd_open(unsigned int gpio)
{
  int fd;
  char buf[MAX_BUF];

  snprintf(buf, sizeof(buf), SYSFS_GPIO_DIR "/gpio%d/value", gpio);
 
  fd = open(buf, O_RDONLY | O_NONBLOCK );
  if (fd < 0) {
    perror("gpio/fd_open");
  }
  return fd;
}

/****************************************************************
 * gpio_fd_close
 ****************************************************************/

int gpio_fd_close(int fd)
{
  return close(fd);
}


/****************************************************************
 * gpio_poll
****************************************************************/

int gpio_poll(int gpio_fd, int timeout)
{
  struct pollfd fdset[1];
  int nfds = 1;
  int rc;
  char buf[MAX_BUF];

  memset((void*)fdset, 0, sizeof(fdset));

  fdset[0].fd = gpio_fd;
  fdset[0].events = POLLPRI;

  rc = poll(fdset, nfds, timeout);

  if (fdset[0].revents & POLLPRI) {
    // dummy read
    read(fdset[0].fd, buf, MAX_BUF);
  }

  return rc;
}
